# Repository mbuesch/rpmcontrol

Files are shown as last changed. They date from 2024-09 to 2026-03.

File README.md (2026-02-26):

# Motor RPM controller - For AVR - In Rust

This project contains the firmware for a motor speed RPM controller based on phase angle control.

It is written in Rust for AVR.

## Features

- PID controller for motor RPM regulation
- Triac control for AC motor speed adjustment
- Speed measurement from a magnet-based speedometer generator
- Temperature sensing for motor and microcontroller
- Safety monitoring and safety shutoff

## Restrictions

The system is currently restricted to 50 Hz mains frequency.
This limit can be lifted, if needed.
Please open an issue if you need support for 60 Hz mains.

## Hardware

- **Microcontroller:** Atmel ATTiny861A
- Open Source PCB

## Building the Firmware

To build the firmware, you need the following tools:

- Rust AVR compiler: A `nightly` compiler is required
- [avr-libc](https://github.com/avrdudes/avr-libc) AVR-specific C library
- `avr-gcc` + `avr-binutils` toolchain (for linking and binary processing: `avr-ld`, `avr-objcopy`, `avr-size`, etc.)
- [avr-postprocess](https://github.com/mbuesch/avr-postprocess) for post-processing the compiled AVR machine code
- [avra](https://github.com/Ro5bert/avra) for assembling AVR assembly code
- Gnu `make`
- [avrdude](https://github.com/avrdudes/avrdude) and [dwdebug](https://github.com/mbuesch/dwire-debug) (optional) for flashing

Once the toolchain is installed, you can build the firmware by running `make`:

```bash
cd firmware
make
```

This will build the project and create the firmware files in the
`firmware/target/avr-attiny861a/release/`
directory.
The final hex file for flashing is
`firmware/target/avr-attiny861a/release/rpmcontrol.post.hex`.

## Flashing the Firmware

The `Makefile` provides targets for flashing the firmware using `avrdude` (for ISP) or `dwdebug` (for debugWire).

### SAFETY PRECAUTIONS: Electrically connecting the programmer device (ISP or debugWire)

**WARNING**:
There is a serious safety risk when connecting the programmer to the microcontroller.
The microcontroller operates at mains voltage, which can be lethal if not handled properly.
The circuit does **not** have galvanic isolation, so there is a direct electrical connection between the ISP/debugWire and the mains voltage.

**BEFORE CONNECTING THE PROGRAMMER:**
Make sure to power the circuit from a safe isolation transformer instead of directly from the mains.
This will provide galvanic isolation from mains voltage.

**IF YOU DON'T FOLLOW THESE SAFETY PRECAUTIONS, YOU RISK SERIOUS ELECTRIC SHOCK, INJURY, DEATH or damage to your equipment.**

### ISP Flashing

First, set the fuses (this only needs to be done once):

```bash
cd firmware
make isp-fuses
```

Then, flash the firmware:

```bash
cd firmware
make isp-flash
```

### debugWire Flashing

To flash the firmware using debugWire:

```bash
cd firmware
make dw-flash
```

## Functional Safety during operation

Note that the AVR microcontroller is **not** a safety-certified controller.
Therefore, this project should not be used in any safety-critical application.

This project implements many safety features that should make it practically safe to use in many applications.
However, the safety features are not guaranteed to be sufficient for all applications and all failure modes and the usual functional safety standards are **not** followed.

**YOU ARE RESPONSIBLE FOR THE SAFETY OF YOUR APPLICATION.**

If you think there is a safety issue with the project, then do not use it.

## Electrical Safety

**THIS PROJECT OPERATES AT MAINS VOLTAGE AND CAN BE LETHAL IF NOT HANDLED PROPERLY.**

If you are not an expert certified in working with mains voltage, then do not use this project.

## License

This project is dual-licensed under either of the following:

*   Apache License, Version 2.0 ([LICENSE-APACHE](LICENSE-APACHE))
*   MIT license ([LICENSE-MIT](LICENSE-MIT))

at your option.

Copyright (C) 2025 - 2026 Michael Büsch <m@bues.ch>

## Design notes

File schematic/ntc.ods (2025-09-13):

Temp C | kOhms
-40 | 186
-35 | 143.1
-30 | 110.8
-25 | 86.39
-20 | 67.79
-15 | 53.53
-10 | 42.54
-5 | 34.01
0 | 27.35
5 | 22.13
10 | 18
15 | 14.72
20 | 12.1
25 | 10
30 | 8.304
35 | 6.929
40 | 5.809
45 | 4.891
50 | 4.137
55 | 3.513
60 | 2.996
65 | 2.565
70 | 2.204
75 | 1.901
80 | 1.645
85 | 1.429
90 | 1.245
95 | 1.089
100 | 0.9549
105 | 0.84
110 | 0.7411
115 | 0.6556
120 | 0.5817
125 | 0.5174
130 | 0.4614
135 | 0.4125
140 | 0.3697
145 | 0.3321
150 | 0.299

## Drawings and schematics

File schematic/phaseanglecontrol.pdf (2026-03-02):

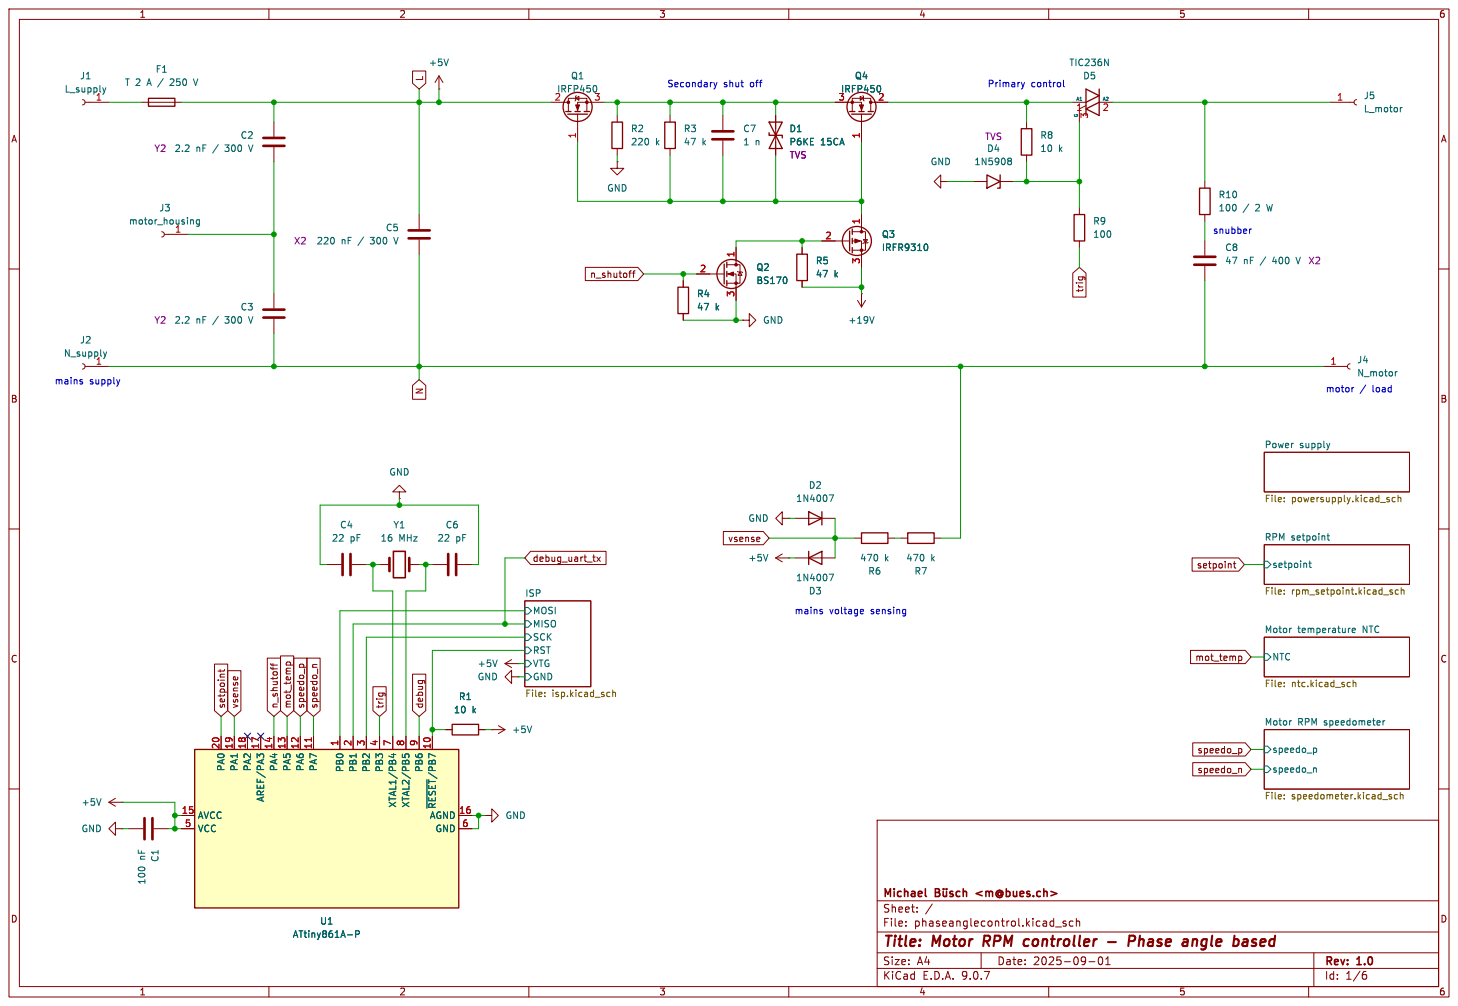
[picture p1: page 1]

setpoint RPM setpoint File: rpm_setpoint.kicad_sch

ISP
SCK RST VTG MOSI GND
+5V GND GND

Id: 1/6 Title: Motor RPM controller - Phase angle based

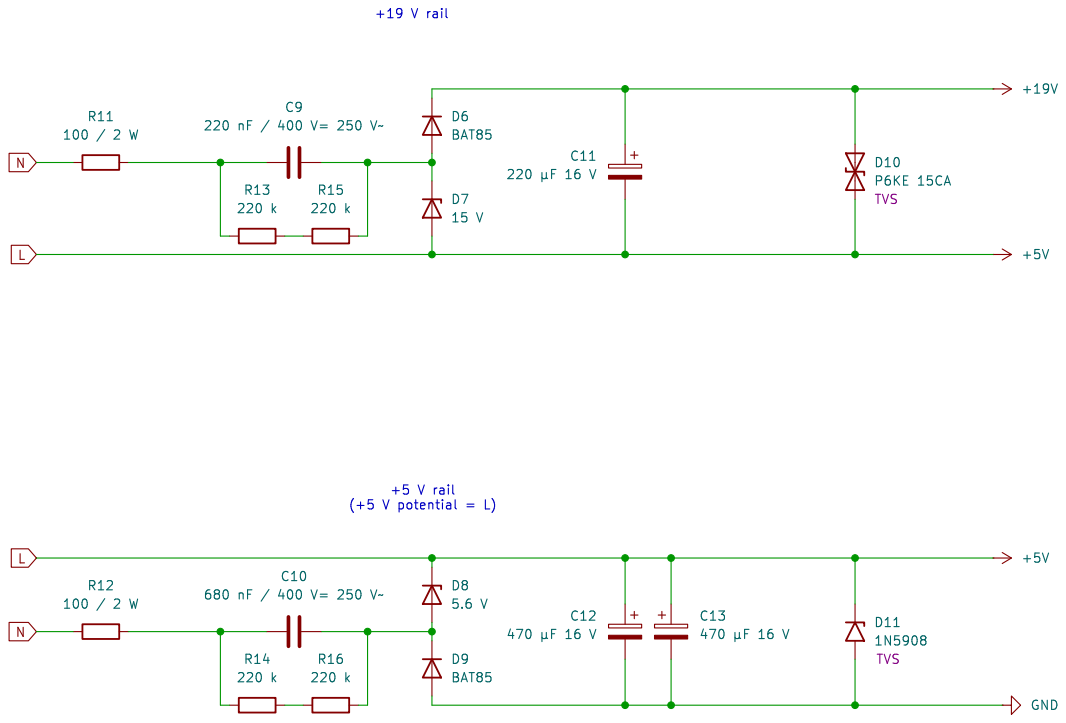
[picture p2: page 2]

Id: 2/6 Title: Motor RPM controller - Power supply

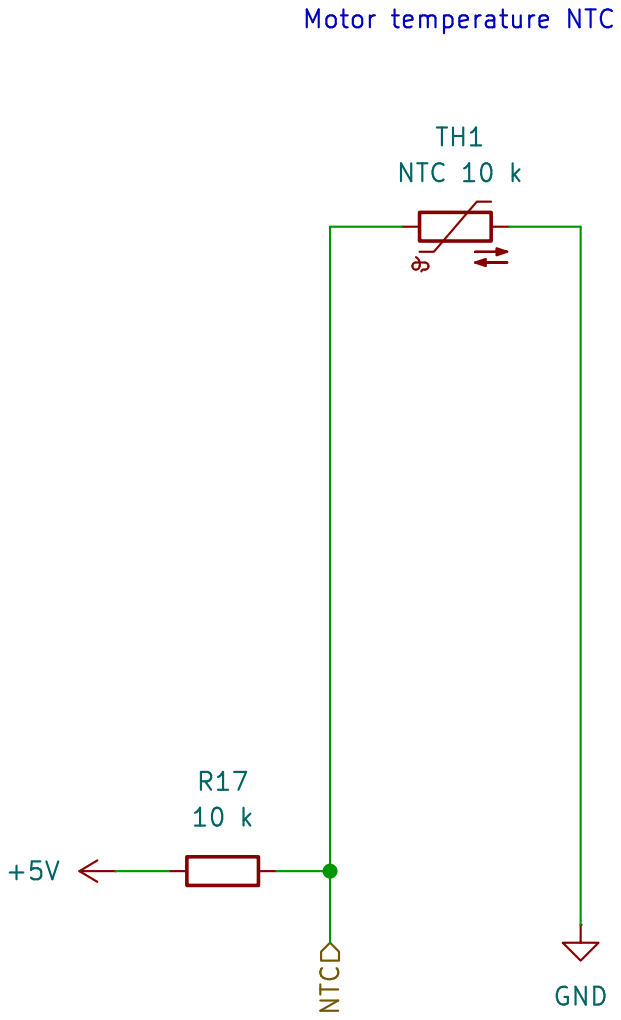
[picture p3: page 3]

Id: 4/6 Title: Motor RPM controller - Motor temperature

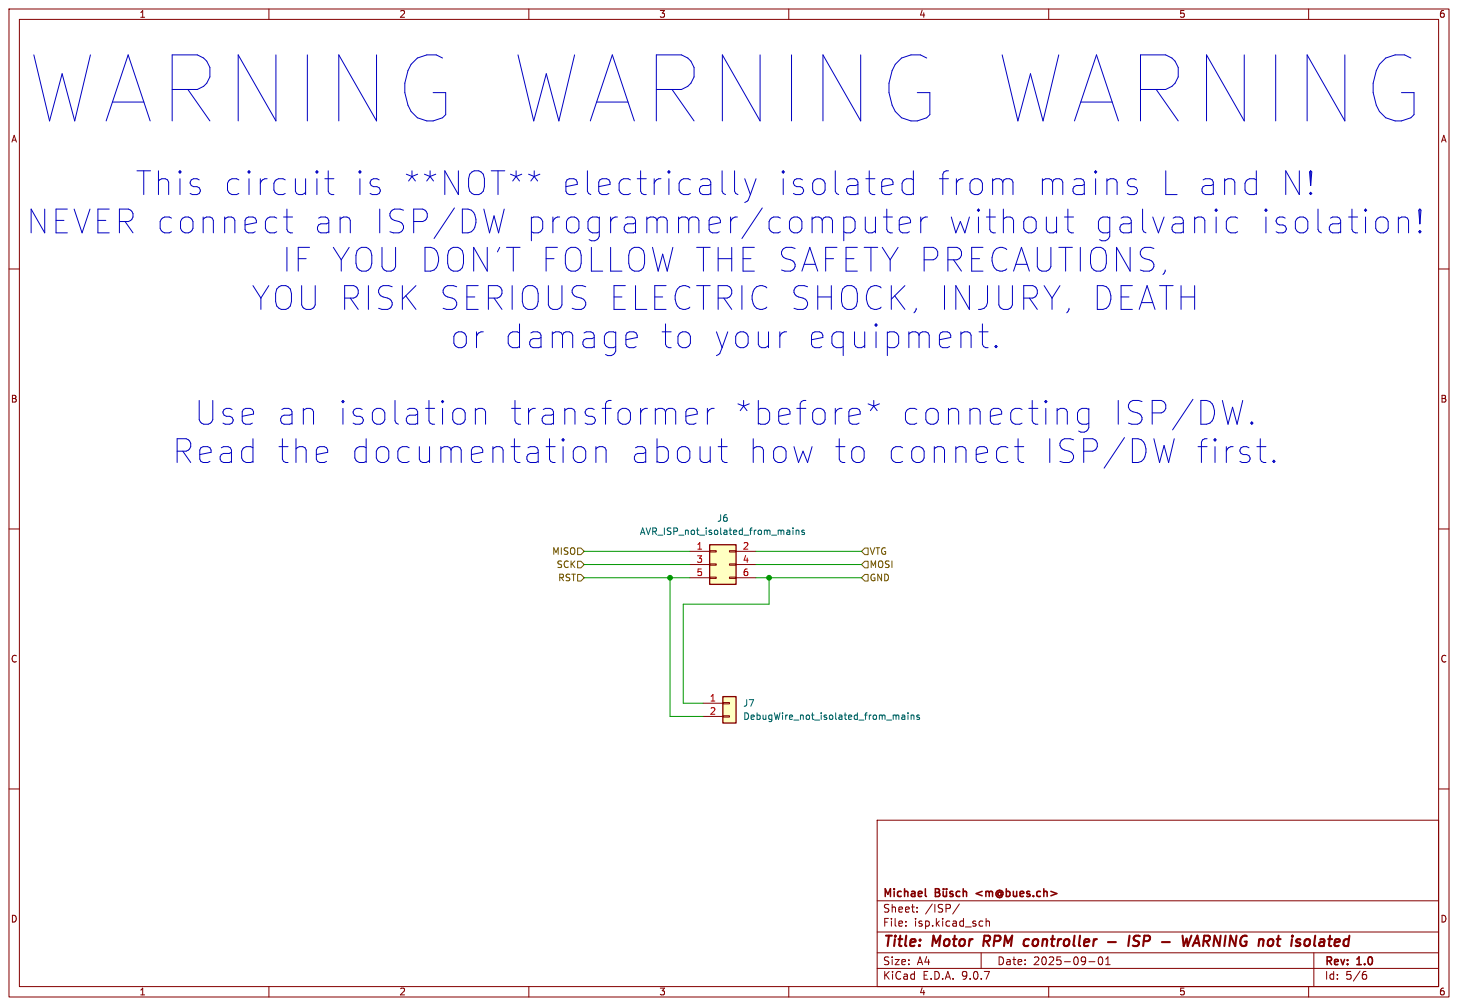
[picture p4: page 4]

VTG MOSI WARNING WARNING WARNING

IF YOU DON'T FOLLOW THE SAFETY PRECAUTIONS,
YOU RISK SERIOUS ELECTRIC SHOCK, INJURY, DEATH

Id: 5/6 Title: Motor RPM controller - ISP - WARNING not isolated

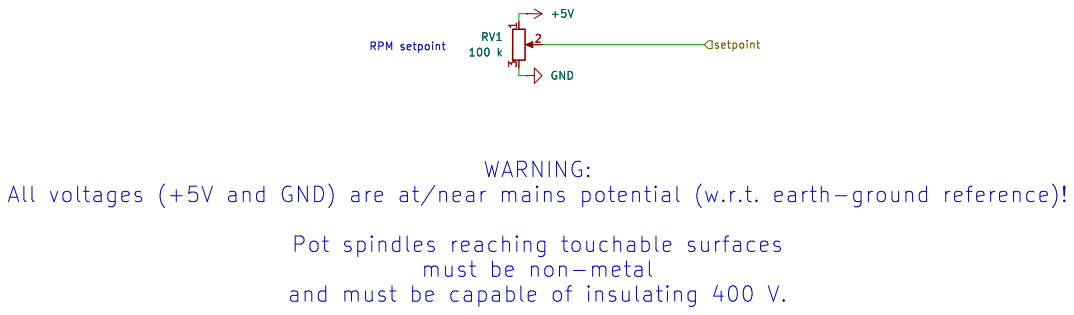
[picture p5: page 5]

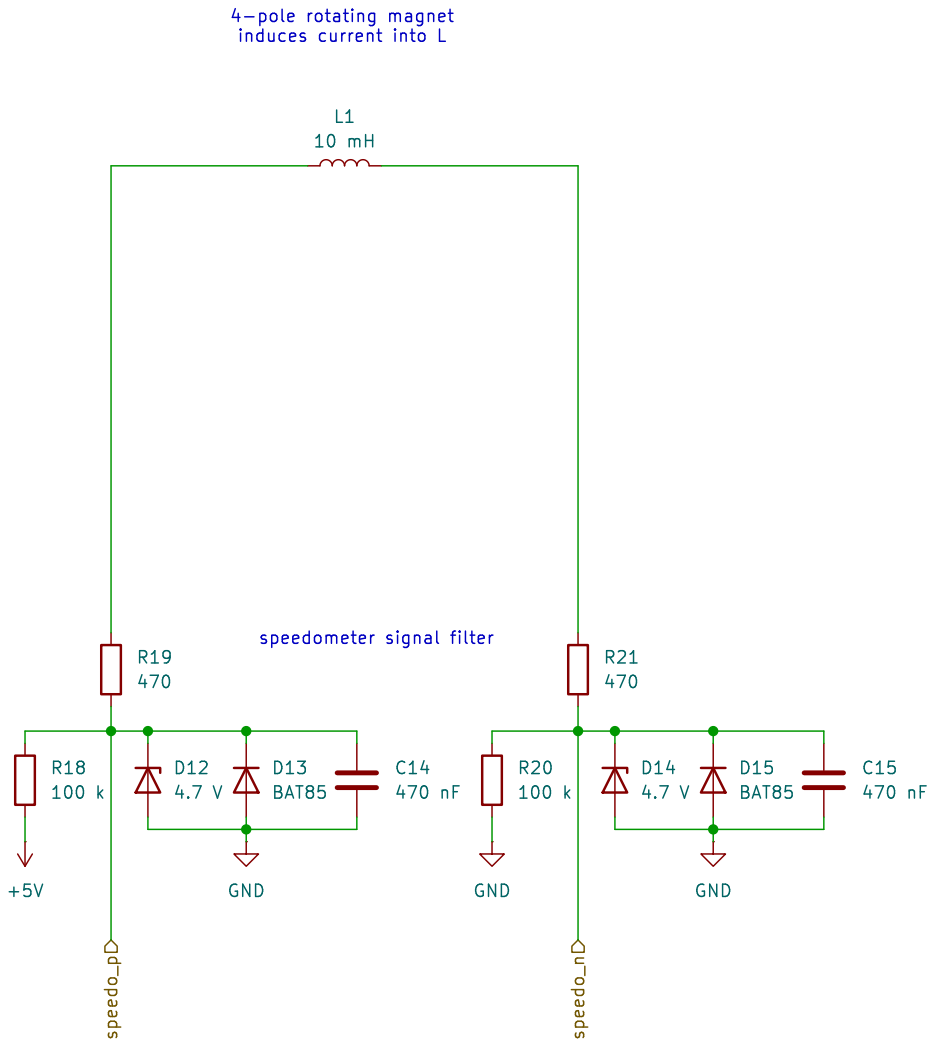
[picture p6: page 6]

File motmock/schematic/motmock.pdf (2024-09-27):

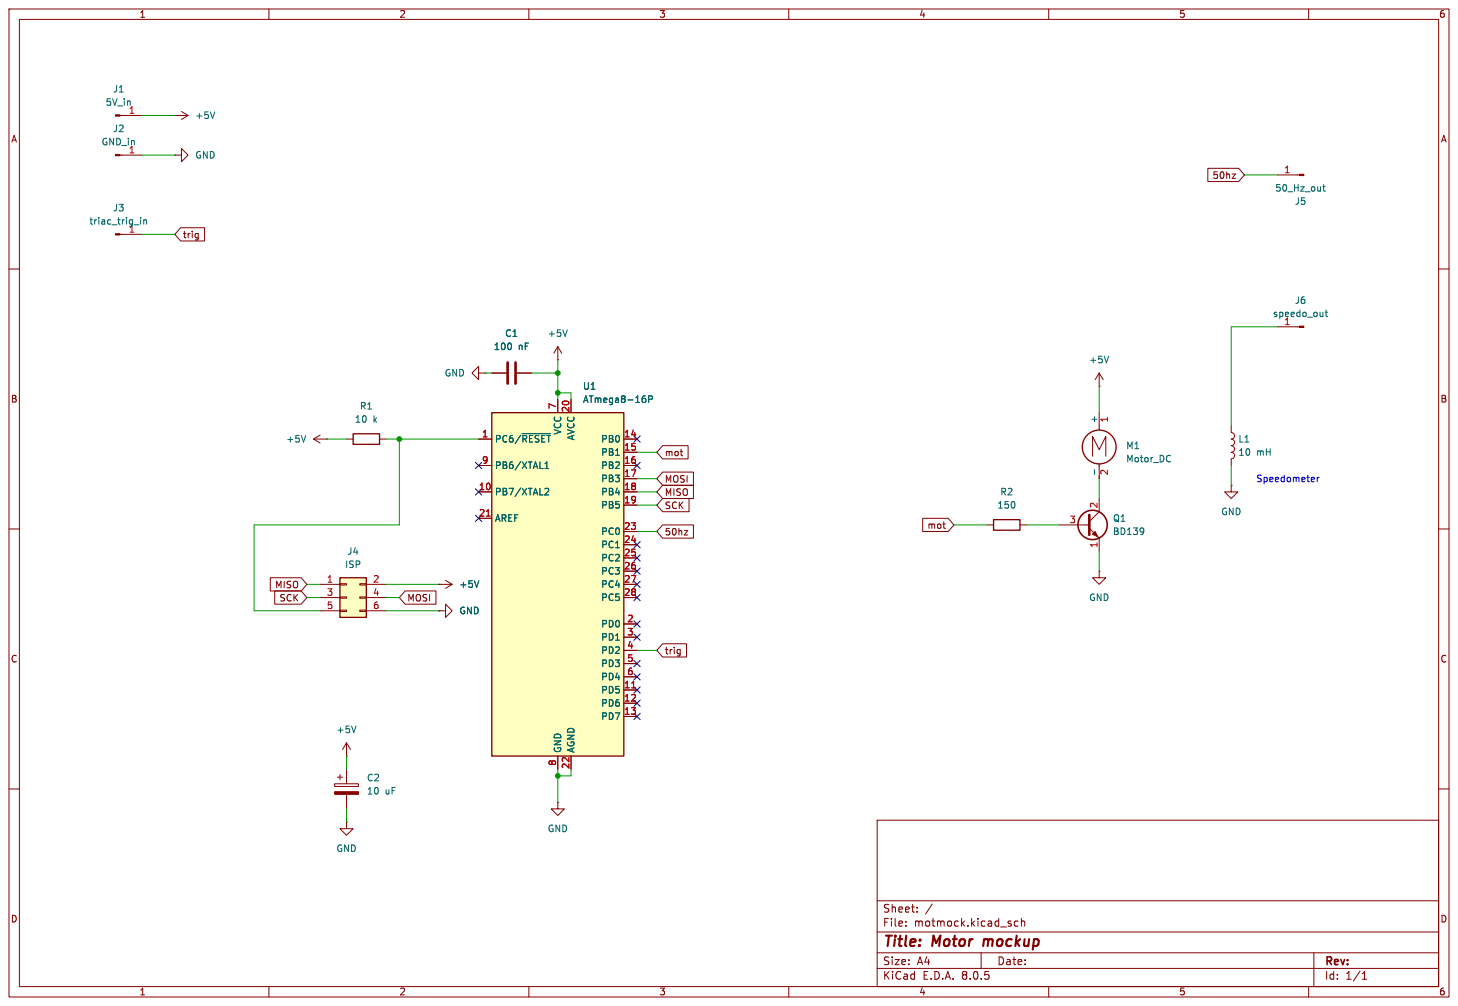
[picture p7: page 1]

Id: 1/1 Title: Motor mockup

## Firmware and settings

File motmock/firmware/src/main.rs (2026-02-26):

// -*- coding: utf-8 -*-
// SPDX-License-Identifier: Apache-2.0 OR MIT
// Copyright (C) 2025 - 2026 Michael Büsch <m@bues.ch>

#![no_std]
#![no_main]
#![feature(abi_avr_interrupt)]
#![feature(asm_experimental_arch)]

use crate::filter::Filter;
use avr_device::atmega8::{PORTB, PORTC, PORTD, Peripherals, TC1, TC2};

mod filter;

/// # Safety
///
/// Must only be called during init with IRQs disabled.
pub unsafe fn ports_init(pb: &PORTB, pc: &PORTC, pd: &PORTD) {
    fn pin_input(_bit: usize) -> u8 {
        0
    }
    fn pin_output(bit: usize) -> u8 {
        1 << bit
    }
    fn pin_low(_bit: usize) -> u8 {
        0
    }
    fn pin_floating(_bit: usize) -> u8 {
        0
    }

    // PORTB
    pb.portb().write(|w| {
        // SAFETY: We are running in init with IRQs disabled.
        unsafe {
            w.bits(
                pin_low(0) | // n/c
                pin_low(1) | // mot
                pin_low(2) | // n/c
                pin_low(3) | // ISP MOSI
                pin_low(4) | // ISP MISO
                pin_low(5), // ISP SCK
            )
        }
    });
    pb.ddrb().write(|w| {
        // SAFETY: We are running in init with IRQs disabled.
        unsafe {
            w.bits(
                pin_output(0) | // n/c
                pin_output(1) | // mot
                pin_output(2) | // n/c
                pin_output(3) | // ISP MOSI
                pin_output(4) | // ISP MISO
                pin_output(5), // ISP SCK
            )
        }
    });

    // PORTC
    pc.portc().write(|w| {
        // SAFETY: We are running in init with IRQs disabled.
        unsafe {
            w.bits(
                pin_low(0) | // 50hz
                pin_low(1) | // n/c
                pin_low(2) | // n/c
                pin_low(3) | // n/c
                pin_low(4) | // n/c
                pin_low(5) | // n/c
                pin_low(6) | // n/c
                pin_low(7), // n/c
            )
        }
    });
    pc.ddrc().write(|w| {
        // SAFETY: We are running in init with IRQs disabled.
        unsafe {
            w.bits(
                pin_output(0) | // 50hz
                pin_output(1) | // n/c
                pin_output(2) | // n/c
                pin_output(3) | // n/c
                pin_output(4) | // n/c
                pin_output(5) | // n/c
                pin_output(6) | // n/c
                pin_output(7), // n/c
            )
        }
    });

    // PORTD
    pd.portd().write(|w| {
        // SAFETY: We are running in init with IRQs disabled.
        unsafe {
            w.bits(
                pin_low(0) | // n/c
                pin_low(1) | // n/c
                pin_floating(2) | // trig
                pin_low(3) | // n/c
                pin_low(4) | // n/c
                pin_low(5) | // n/c
                pin_low(6) | // n/c
                pin_low(7), // n/c
            )
        }
    });
    pd.ddrd().write(|w| {
        // SAFETY: We are running in init with IRQs disabled.
        unsafe {
            w.bits(
                pin_output(0) | // n/c
                pin_output(1) | // n/c
                pin_input(2) |  // trig
                pin_output(3) | // n/c
                pin_output(4) | // n/c
                pin_output(5) | // n/c
                pin_output(6) | // n/c
                pin_output(7), // n/c
            )
        }
    });
}

const TIMER1_DUTYMAX: u16 = 0xFF;

#[rustfmt::skip]
fn timer1_init(tc1: &TC1) {
    tc1.icr1().write(|w| w.set(TIMER1_DUTYMAX));
    tc1.ocr1a().write(|w| w.set(0x00));
    tc1.tccr1a().write(|w| {
        w.com1a().match_clear()
         .com1b().disconnected()
         .wgm1().set(2)
    });
    tc1.tccr1b().write(|w| {
        w.cs1().prescale_64()
         .wgm1().set(2)
    });
}

fn timer1_duty(tc1: &TC1, duty: u16) {
    tc1.ocr1a().write(|w| w.set(duty));
    if tc1.tcnt1().read().bits() > duty {
        tc1.tcnt1().write(|w| w.set(0));
    }
}

const TIMER2_MAX: u8 = 78;
const TIMER2_CUTOFF: u8 = 2;

#[rustfmt::skip]
fn timer2_init(tc2: &TC2) {
    // Timer2 init; ctc, 100 Hz.
    tc2.ocr2().write(|w| w.set(TIMER2_MAX));
    tc2.tccr2().write(|w| {
        w.cs2().prescale_1024()
         .wgm20().clear_bit()
         .wgm21().set_bit()
    });
}

fn timer2_event(tc2: &TC2) -> bool {
    let ocf = tc2.tifr().read().ocf2().bit();
    if ocf {
        tc2.tifr().write(|w| w.ocf2().set_bit());
    }
    ocf
}

fn timer2_value(tc2: &TC2) -> u8 {
    tc2.tcnt2().read().bits().min(TIMER2_MAX)
}

#[avr_device::entry]
fn main() -> ! {
    let dp = Peripherals::take().unwrap();

    // SAFETY: We are running in init with IRQs disabled.
    unsafe {
        ports_init(&dp.PORTB, &dp.PORTC, &dp.PORTD);
    }
    timer1_init(&dp.TC1);
    timer2_init(&dp.TC2);

    let mut triggered = false;
    let mut duty_filter = Filter::new();
    const DUTY_FILTER_SHIFT: u8 = 2;
    loop {
        // Simulated mains zero crossing.
        let zerocrossing = timer2_event(&dp.TC2);

        // 50 Hz output.
        dp.PORTC
            .portc()
            .modify(|r, w| w.pc0().bit(r.pc0().bit() ^ zerocrossing));

        // Triac trigger input.
        if zerocrossing {
            if !triggered {
                // No trigger -> Turn PWM off.
                let duty = duty_filter.run(0, DUTY_FILTER_SHIFT);
                timer1_duty(&dp.TC1, duty);
            }
            triggered = false;
        }
        let trig = !dp.PORTD.pind().read().pd2().bit();
        if trig && !triggered {
            triggered = true;

            // Output PWM proportionally to triac trigger time.
            let mut val: u8 = TIMER2_MAX - timer2_value(&dp.TC2);
            if val <= TIMER2_CUTOFF {
                val = 0;
            }
            let val: u16 = val.into();

            let duty = val * (TIMER1_DUTYMAX + 1) / (TIMER2_MAX as u16 + 1);
            let duty = (duty * 3) / 4; // reduce
            let duty = duty_filter.run(duty, DUTY_FILTER_SHIFT);

            timer1_duty(&dp.TC1, duty);
        }
    }
}

#[panic_handler]
fn panic(_: &core::panic::PanicInfo) -> ! {
    loop {}
}

// vim: ts=4 sw=4 expandtab

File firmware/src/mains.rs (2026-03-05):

// -*- coding: utf-8 -*-
// SPDX-License-Identifier: Apache-2.0 OR MIT
// Copyright (C) 2025 - 2026 Michael Büsch <m@bues.ch>

use crate::{
    calibration::mains::{MAINS_HZ, MAINS_NEXT_CAPTURE},
    ports::{PORTA, PortOps as _},
    timer::{LargeTimestamp, RelLargeTimestamp, timer_get_large, timer_get_large_cs},
};
use avr_context::{CriticalSection, IrqCtx, MainCtx, MainCtxCell, Mutex, with_cs};
use avr_q::{Q7p8, q7p8};
use core::cell::Cell;

/// Mains sine wave period.
pub const MAINS_PERIOD_MS: Q7p8 = get_mains_period_ms_q();
/// Mains sine wave period.
pub const MAINS_PERIOD: RelLargeTimestamp = get_mains_period_timestamp();

/// Mains sine wave half-wave length.
pub const MAINS_HALFWAVE_DUR_MS: Q7p8 = MAINS_PERIOD_MS.const_div(q7p8!(const 2));
/// Mains sine wave half-wave length.
pub const MAINS_HALFWAVE_DUR: RelLargeTimestamp = MAINS_PERIOD.div(2);

/// Mains sine wave quarter-wave length.
pub const MAINS_QUARTERWAVE_DUR: RelLargeTimestamp = MAINS_PERIOD.div(4);

const fn get_mains_period_ms_q() -> Q7p8 {
    match MAINS_HZ {
        50 => q7p8!(const 20),
        _ => panic!("Unsupported mains frequency."),
    }
}

const fn get_mains_period_timestamp() -> RelLargeTimestamp {
    match MAINS_HZ {
        50 => RelLargeTimestamp::from_millis(20),
        _ => panic!("Unsupported mains frequency."),
    }
}

fn read_vsense(cs: CriticalSection<'_>) -> bool {
    PORTA.get(cs, 1)
}

#[derive(Clone, Copy, PartialEq, Eq)]
pub enum Phase {
    Notsync,
    NegHalfwave,
    PosHalfwave,
}

#[derive(Clone, Copy, PartialEq, Eq)]
pub enum PhaseUpdate {
    NotChanged,
    Changed,
}

pub struct Mains {
    prev_vsense: MainCtxCell<bool>,
    phase: MainCtxCell<Phase>,
    phaseref: MainCtxCell<LargeTimestamp>,
}

impl Mains {
    pub const fn new() -> Self {
        Self {
            prev_vsense: MainCtxCell::new(false),
            phase: MainCtxCell::new(Phase::Notsync),
            phaseref: MainCtxCell::new(LargeTimestamp::new()),
        }
    }

    pub fn init(&self, _m: &MainCtx<'_>, _now: LargeTimestamp) {
        // Nothing do to.
    }

    /// Run mains vsense pin reading and evaluation.
    pub fn run(&self, m: &MainCtx<'_>) -> PhaseUpdate {
        let mut ret = PhaseUpdate::NotChanged;

        let (vsense, vsense_stamp) =
            with_cs(|cs| (VSENSE.borrow(cs).get(), VSENSE_STAMP.borrow(cs).get()));

        match self.phase.get(m) {
            Phase::Notsync | Phase::NegHalfwave => {
                if !self.prev_vsense.get(m) && vsense {
                    self.phaseref.set(m, vsense_stamp);
                    self.phase.set(m, Phase::PosHalfwave);
                    ret = PhaseUpdate::Changed;
                }
            }
            Phase::PosHalfwave => {
                let nextref = self.phaseref.get(m) + MAINS_HALFWAVE_DUR;
                let now = timer_get_large();
                if now >= nextref {
                    self.phaseref.set(m, nextref);
                    self.phase.set(m, Phase::NegHalfwave);
                    ret = PhaseUpdate::Changed;
                }
            }
        }
        self.prev_vsense.set(m, vsense);

        ret
    }

    pub fn get_phase(&self, m: &MainCtx<'_>) -> Phase {
        self.phase.get(m)
    }

    pub fn get_phaseref(&self, m: &MainCtx<'_>) -> LargeTimestamp {
        self.phaseref.get(m)
    }

    pub fn get_time_since_zerocrossing(&self, m: &MainCtx<'_>) -> Option<RelLargeTimestamp> {
        if self.phase.get(m) == Phase::Notsync {
            None
        } else {
            Some(timer_get_large() - self.phaseref.get(m))
        }
    }
}

static VSENSE: Mutex<Cell<bool>> = Mutex::new(Cell::new(false));
static VSENSE_STAMP: Mutex<Cell<LargeTimestamp>> = Mutex::new(Cell::new(LargeTimestamp::new()));

pub fn irq_handler_pcint(c: &IrqCtx) {
    let cs = c.cs();

    let now = timer_get_large_cs(cs);
    let vsense = read_vsense(cs);

    let prev_vsense = VSENSE.borrow(cs).get();
    let prev_stamp = VSENSE_STAMP.borrow(cs).get();

    if vsense != prev_vsense && now >= prev_stamp + MAINS_NEXT_CAPTURE {
        VSENSE.borrow(cs).set(vsense);
        VSENSE_STAMP.borrow(cs).set(now);
    }
}

// vim: ts=4 sw=4 expandtab

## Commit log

2024-08-29 Update wdt time
    [phaseanglecontrol.kicad_sch]
2024-08-30 Use timer0 for sys timer
2024-09-13 Fix f to trig
    [system.rs]
2024-09-21 Update avr-device crate
2024-09-24 Add motmock base
    [motmock.kicad_pcb, motmock.kicad_sch]
2024-09-27 Add motor mock base
    [motmock.kicad_sch]
2024-12-28 motmock: Add missing safety comments
    [main.rs]
2025-01-07 schematic: Add schottky to speedo input
    [phaseanglecontrol.kicad_sch]
2025-01-10 speedo: Fix analog edge eval
    [analog.rs, speedo.rs, system.rs]
2025-01-11 pi: Add reset flag
    [system.rs]
2025-01-16 Fix ANA_COMP IRQ for attiny861a
    [analog.rs]
2025-01-16 systimer: Use timer 1
2025-01-18 Add uart tx
2025-05-30 firmware: Many small fixes
    [analog.rs, debug.rs, main.rs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]
2025-05-30 Update schematic
    [isp.kicad_sch, phaseanglecontrol.kicad_sch, rpm_generator.kicad_sch]
2025-05-30 Fix num debug signals
    [debug.rs]
2025-08-10 Update power supply
    [phaseanglecontrol.kicad_sch]
2025-08-11 Fix incorrect call to mains eval
    [system.rs]
2025-08-12 timer: Add const div
2025-08-12 triac: Re-trigger during low trigger voltages
2025-08-13 Move timer conversion code
2025-08-14 Add filter
2025-08-14 speedo: Add filter
2025-08-14 filter: Remove unused reset
2025-08-14 Add temperature mod
2025-08-14 fixpt: Add zero macro
    [system.rs]
2025-08-14 filter: Use zero macro
2025-08-14 sys: Reset controller I
    [system.rs]
2025-08-15 adc: Discard first result
2025-08-15 Increase speedo filter
2025-08-15 sys: Add support for 24000 RPM
2025-08-15 sys: Add setpoint filter
2025-08-16 filter: Add reset and get
2025-08-16 sys: Add filter to store speed
2025-08-16 Use PID controller instead of PI
2025-08-17 schematic: New speedo signal processing
    [phaseanglecontrol.kicad_sch]
2025-08-17 Put the PID calc at mains sine max
2025-08-19 fuses: Reduce BOD voltage
2025-08-21 timer: Add support for abs - rel => abs
2025-08-21 Add support for timer interrupt
2025-08-21 triac: Use timer interrupt
2025-08-22 timer: rustfmt
2025-08-22 timer: Add const sub
2025-08-22 timer: Make all add/sub const
2025-08-22 adc: Remove unused channels
2025-08-22 sys: Fix state handling
    [system.rs]
2025-09-01 Update schematics
    [isp.kicad_sch, ntc.kicad_sch, phaseanglecontrol.kicad_sch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]
2025-09-05 Fix uc temp ref
    [analog.rs]
2025-09-07 Fix uc temp sensor
    [analog.rs, temp.rs]
2025-09-07 Fix phase angle conversion
    [system.rs]
2025-09-07 mock: Add filter
2025-09-08 temp: Add filters
2025-09-08 filter: Use big fixpt
2025-09-08 temp: Increase filter
2025-09-12 mains: Export mains freq as Fixpt
    [mains.rs]
2025-09-12 Add power-on check
2025-09-12 pid: Add neg lim
2025-09-12 Fix trig offset calc
    [system.rs]
2025-09-13 debug: Add run button
2025-09-13 Add ntc curve docs
    [ntc.ods]
2025-09-14 speedo: Avoid mul overflow
    [speedo.rs]
2025-09-14 Update avr-device
2025-09-14 motmock: Update avr-device
2025-09-15 speedo: Avoid div by zero
    [speedo.rs]
2025-09-21 Calc setpoint and rpm as big-fixpt
    [system.rs]
2025-09-22 timer: Force inline conversions
2025-09-25 speedo: Remove primary filter
2025-09-26 Calc setpoint as Fixpt
    [system.rs]
2025-09-26 filter: Store result
2025-09-27 schematic: Add TVS
    [powersupply.kicad_sch]
2025-09-27 analog: Report failure to monitoring
    [analog.rs]
2025-09-27 main: Avoid costly Peripherals::take()
    [main.rs]
2025-09-27 schematic: Update .gitignore
2025-10-12 filter: Avoid one division
2025-10-12 filter: Minor cleanup
2025-10-12 timer: Force no-inline
2025-10-12 Move timer init
2025-10-13 schematic: Add 2nd shutoff biasing
    [ntc.kicad_sch, phaseanglecontrol.kicad_sch, powersupply.kicad_sch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]
2025-10-13 sys: Use port toggle to toggle debug pin
2025-10-13 pocheck: Add debug pin
2025-10-13 schematic: Increase biasing
    [phaseanglecontrol.kicad_sch]
2025-10-13 timer: Add cancel function
2025-10-13 triac: Cancel timers on transitions
2025-10-13 triac: Cancel timer on shutoff
2025-10-18 int24: Fix special mul case
2025-11-16 Add TVS to tirac gate
    [ntc.kicad_sch, phaseanglecontrol.kicad_sch, powersupply.kicad_sch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]
2025-11-16 schematic: Add DW pinheader
    [isp.kicad_sch]
2025-11-16 Use nop3 from avr-device
2025-11-23 schematic: Minor updates
    [phaseanglecontrol.kicad_sch]
2026-02-21 Move calibration data to own module
2026-02-21 reset: Disable interrupts
2026-02-21 Move temp calibration
2026-02-21 timer: Add doc comments
2026-02-21 readme: Add 50Hz info
2026-02-21 timer: Optimize cs handling
2026-02-21 Optimize timer API
2026-02-21 Add timer API
2026-02-22 timer: Rename ms conversion
2026-02-23 speedo: timeout on error
    [calibration.rs, system.rs]
2026-02-23 ring: Add power-of-two assertion
2026-02-26 schematic: Add uart tx
    [phaseanglecontrol.kicad_sch]
2026-02-26 Enable pocheck debug pin by default
2026-02-26 temp: Fix broken hysteresis
    [calibration.rs, temp.rs]
2026-02-28 filter: Allow bigger div
2026-02-28 cal: Update cal for real motor
2026-02-28 mains: Move to calibration
2026-03-01 speedo: Use filter instead of mov avg
2026-03-01 filter: Add doc
2026-03-02 schematic: Update trig resistor
    [isp.kicad_sch, phaseanglecontrol.kicad_sch, rpm_setpoint.kicad_sch]
2026-03-02 schematic: Minor cleanups
    [phaseanglecontrol.kicad_sch, powersupply.kicad_sch]
2026-03-06 Add 2nd order speedo filter
2026-04-18 Update kicad
    [isp.kicad_sch, ntc.kicad_sch, phaseanglecontrol.kicad_sch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]
2026-04-18 schematic: Fix ERC warnings
    [ntc.kicad_sch, powersupply.kicad_sch, rpm_setpoint.kicad_sch]
2026-04-19 schematic: Assign some footprints
    [ntc.kicad_sch, phaseanglecontrol.kicad_sch, powersupply.kicad_sch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]
